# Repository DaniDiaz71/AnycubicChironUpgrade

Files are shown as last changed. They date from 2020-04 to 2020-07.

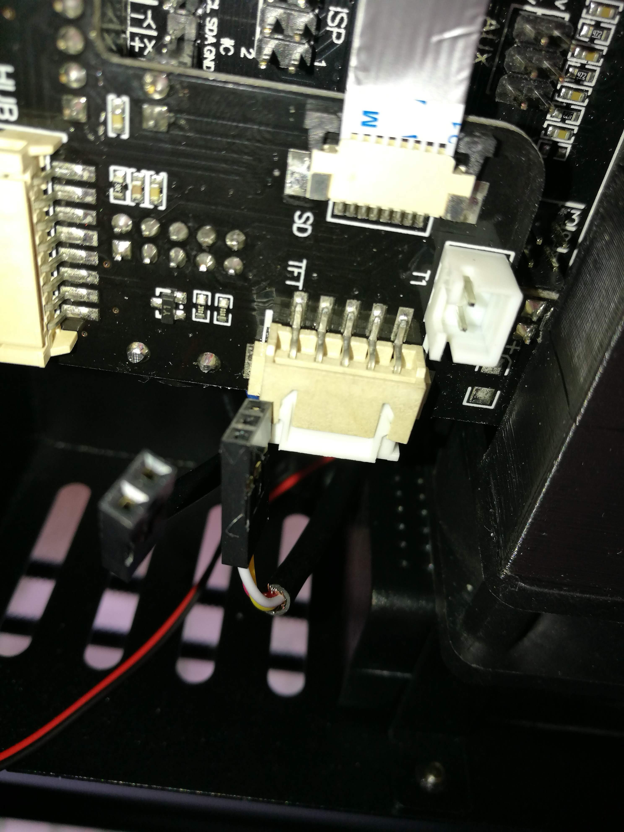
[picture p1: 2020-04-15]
Step 01 - Electronics disassemble/IMG_20200413_175611.jpg

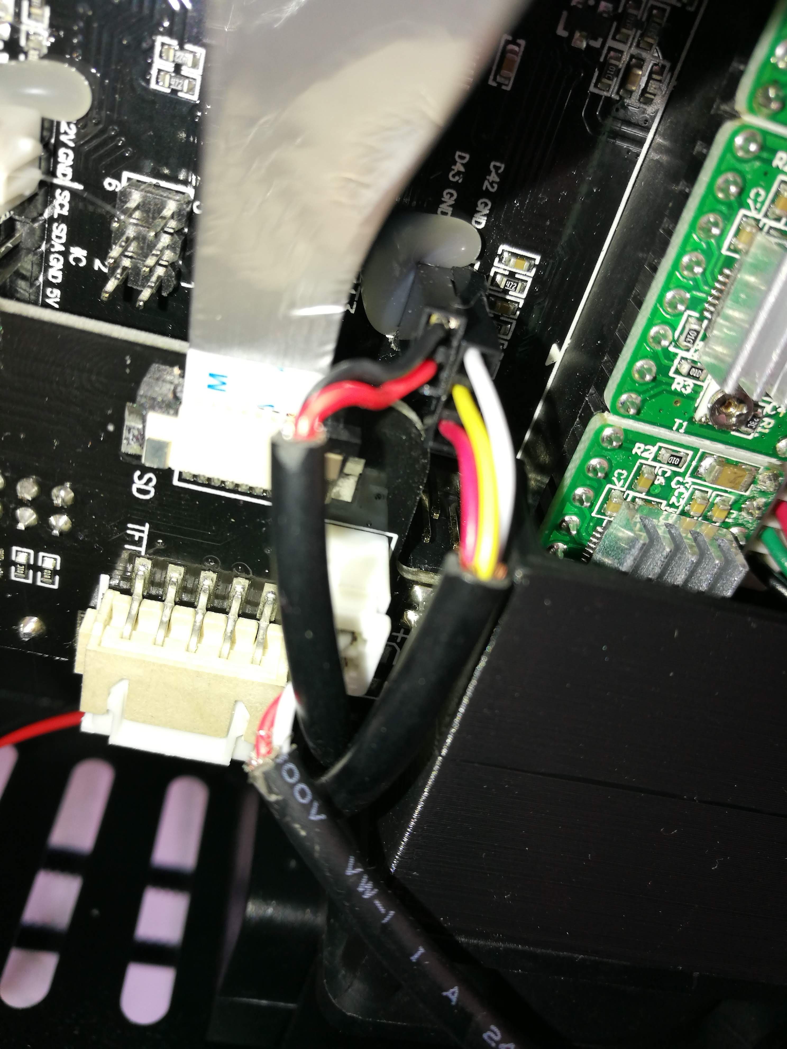
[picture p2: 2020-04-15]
Step 01 - Electronics disassemble/IMG_20200413_175152.jpg

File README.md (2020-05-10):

# AnycubicChironUpgrade

Documentation and other stuff about how upgrade Anycubic Chiron 3D printer from 8 bits to 32 bits electronics, including upgrade stepper drivers to TMC2208. Then i'll configure Marlin.

Work still in progress...

Step 01 - Done!

Step 02 - Done!

Step 03 - Done! 

Step 04 - Done! 

Step in progress - Adding stock display functions to Marlin 2.0.x, there are a lot of work done by dkoch83 at https://github.com/dkoch83/Marlin-1.1.9_Anycubic_Chiron.

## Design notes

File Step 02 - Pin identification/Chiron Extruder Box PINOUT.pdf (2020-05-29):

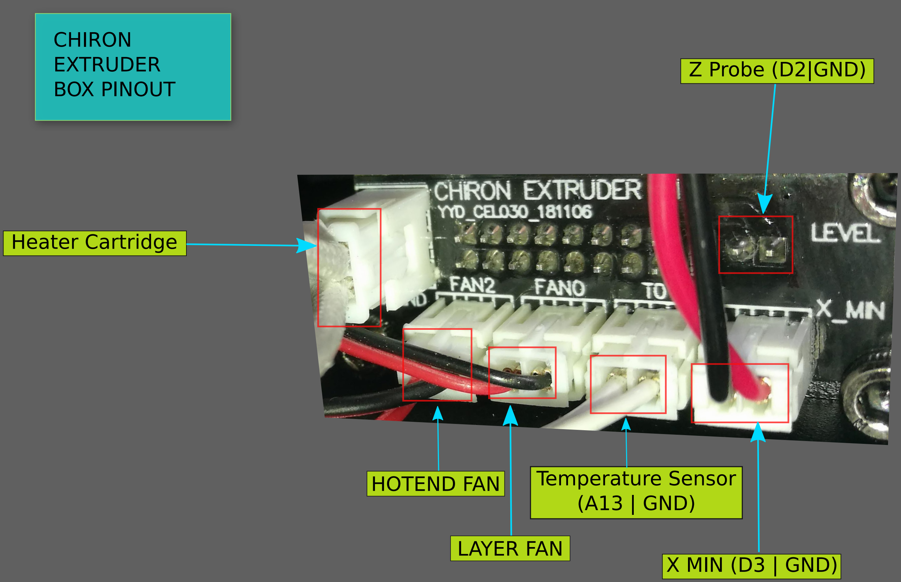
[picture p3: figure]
Heater Cartridge; Z Probe (D2|GND); X MIN (D3 | GND); Temperature Sensor (A13 | GND); LAYER FAN; HOTEND FAN; CHIRON EXTRUDER BOX PINOUT

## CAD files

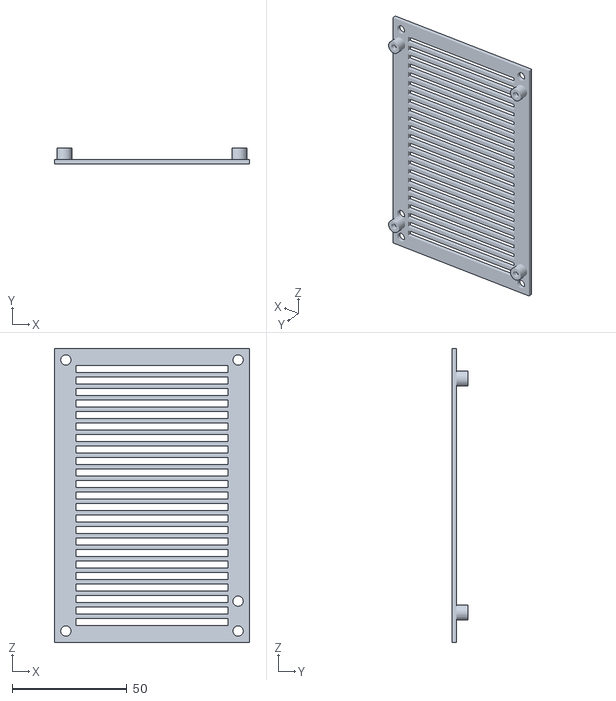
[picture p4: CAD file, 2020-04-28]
Step 03 - Motherboard mount adapter/Chiron Adaptation Mount SKR 1.3 v4.stl
85.0 x 7.00 x 128.0

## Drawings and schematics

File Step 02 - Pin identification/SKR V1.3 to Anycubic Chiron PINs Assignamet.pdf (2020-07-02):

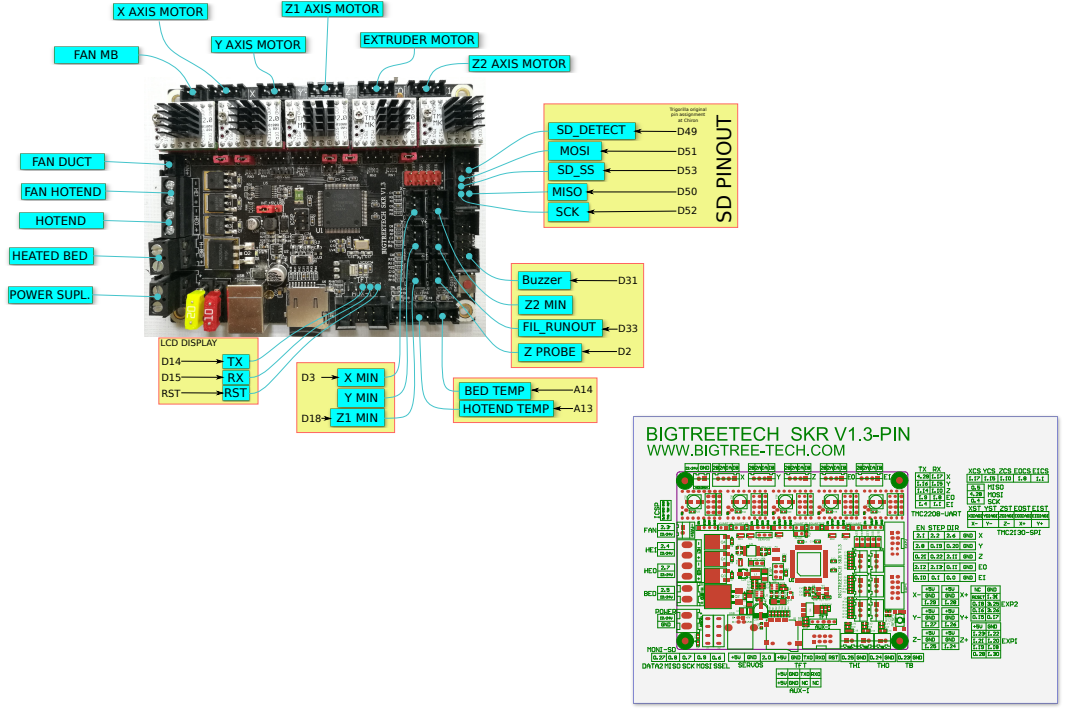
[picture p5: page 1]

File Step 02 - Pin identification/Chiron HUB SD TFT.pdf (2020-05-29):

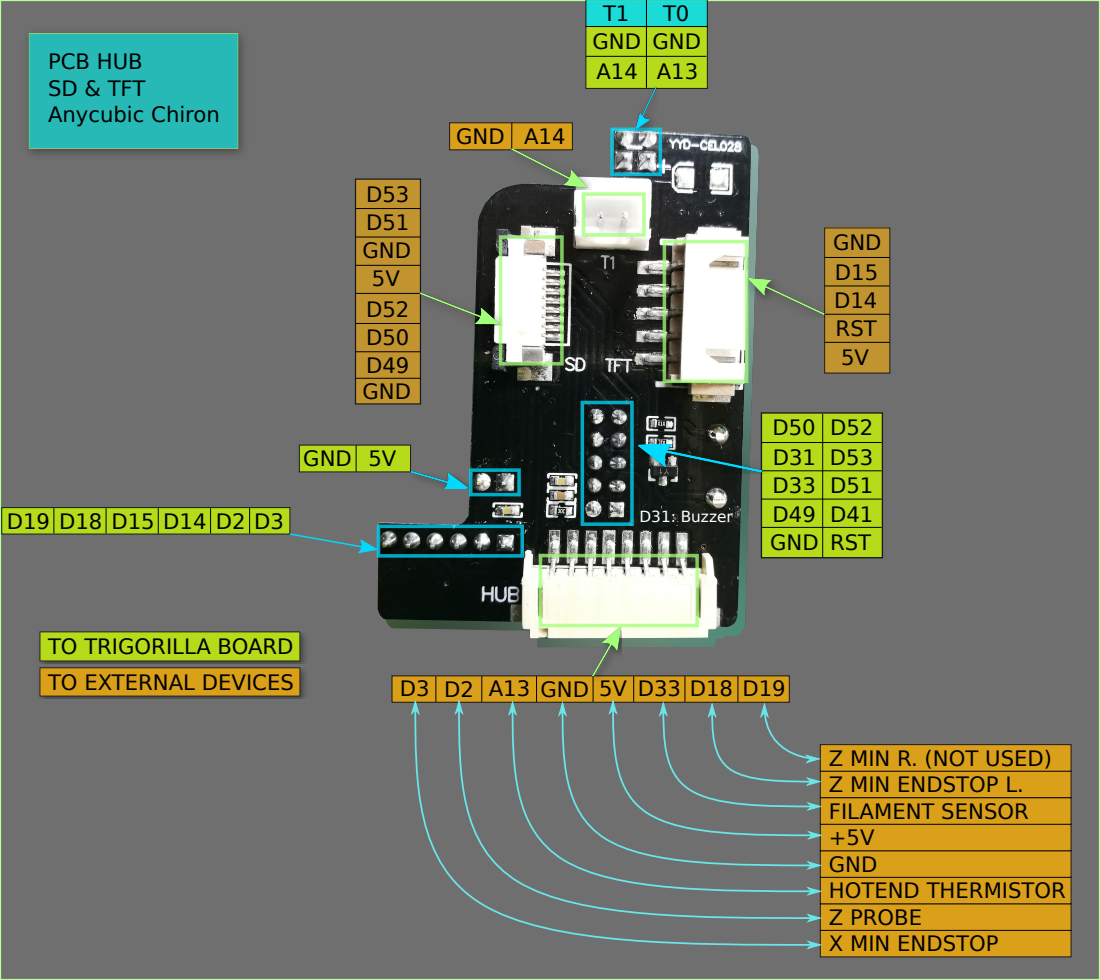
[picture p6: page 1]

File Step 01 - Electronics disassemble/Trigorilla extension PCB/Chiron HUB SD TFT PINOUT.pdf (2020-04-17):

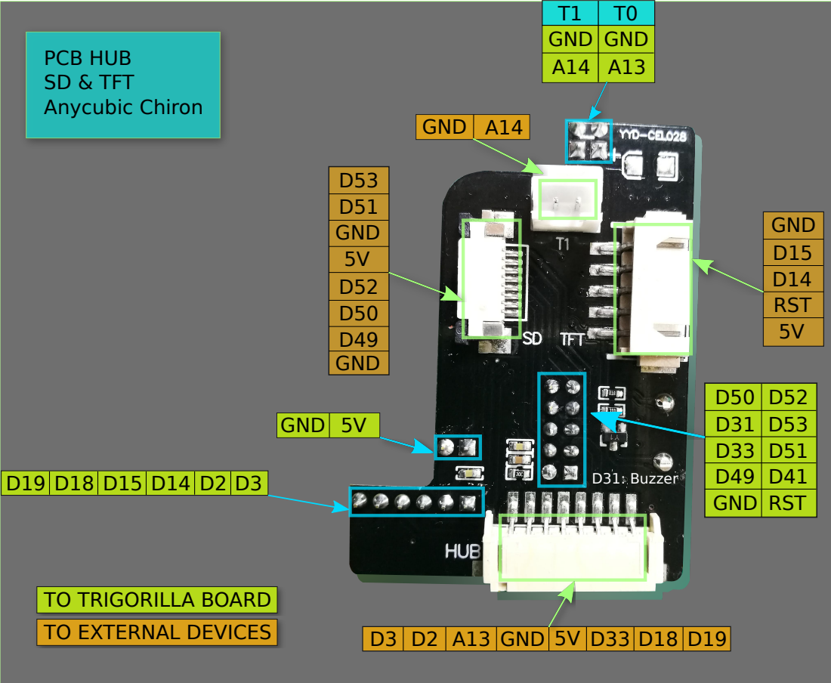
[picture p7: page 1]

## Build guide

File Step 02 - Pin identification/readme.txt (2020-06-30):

Step 02 - Pin identification

In this files are information about non standar pins (TFT, SD, HUB), in particular HUB pin identification.

Chiron HUB SD TFT.svg - Inkscape file with pins from and to Trigorilla board at HUB PCB.
Chiron Extruder Box PINOUT.svg - Inkscape file with pins at hotend box.
New HUB SD TFT PCB to SKR v1.3.fzz - Fritzing file with an small PCB to adapt HUB PCB to SKR v1.3. It's a simple way extract signals.
SKR V1.3 to Anycubic Chiron PINs Assignamet.svg - Inkscape file, pin assingment at SKR v1.3.

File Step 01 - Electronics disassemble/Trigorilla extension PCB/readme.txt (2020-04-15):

This PCB (ref. YYD-CEL028) is over mainboard connecting some pins to SD card reader, heated bed (T1), TFT and other stuff.

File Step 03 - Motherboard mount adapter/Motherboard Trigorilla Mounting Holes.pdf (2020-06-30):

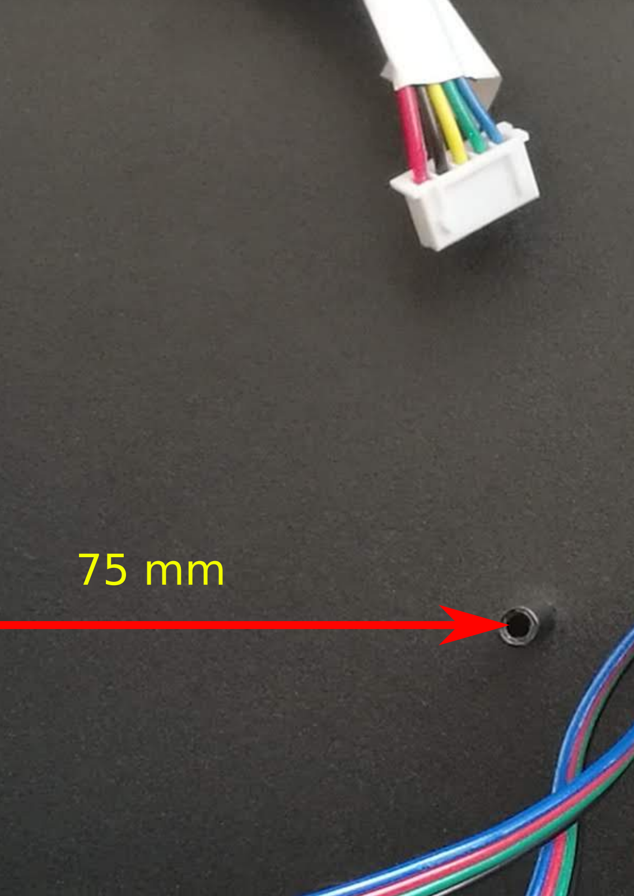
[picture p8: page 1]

75 mm

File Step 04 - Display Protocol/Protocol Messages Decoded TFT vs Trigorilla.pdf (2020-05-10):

### Trigorilla messages after reset

TFT Responds | Trigorilla Sends | Meaning
| | Main board reset
| J12\r\n | Ready

### Periodic update (1.1s) from display to Trigorilla

TFT Request | Trigorilla Response | Meaning
| | A1 → Seted hotend temp (e.g. 200ºC). A2 → Current bed temp (e.g. 50ºC). A3 → Seted bed temp (e.g. 100ºC). A4 → Fan speed (e.g. 1%).

### Query for SD files (Print option)

TFT Request | Trigorilla Response | Meaning
A8' 'S0' '\r\n | J02\r\n | Query [A8] for SD [S0] files but no SD [J02].
| J00\r\n | SD inserted notify [J00]
| J01\r\n | SD extracted notify [J01]
A8' 'S0' '\r\n | | Query for SD files, 3 files in SD.

### Access to Temperature option (Menu>Setup>Temp)

TFT Request | Trigorilla Response | Meaning
A0\r\nA2\r\n

### Access to Motor off option (Menu>Setup>Motor)

TFT Request | Trigorilla Response | Meaning
A19\r\n | \r\n | Turn off motors

### Access to Speed option (Menu>Setup>Speed)

TFT Request | Trigorilla Response | Meaning
| | Query colling fan speed [A4] Query printing rate [A20]
A18' 'S50\r\n | \r\n
A20' 'S120\r\n | \r\n

### Access to Home (Menu>Tools>Auto Home)

TFT Request | Trigorilla Response | Meaning
A21' 'C\r\n | | Home all axis
A21' 'X\r\n | | Home X axis
A21' 'Y\r\n | | Home Y axis
A21' 'Z\r\n | | Home Z axis

### Access to Home (Menu>Tools>Cooling)

TFT Request | Trigorilla Response | Meaning
A25\r\n | J12\r\n | Set hotend cooling

### Access to Home (Menu>Tools>Move Axis)

TFT Request | Trigorilla Response | Meaning
A21' 'C\r\n | | Home all axis
| \r\n | Move X axis 10mm; Speed L
| \r\n | Move X axis -10mm; Speed L
| \r\n | Move X axis 10mm; Speed M
| \r\n | Move X axis -10mm; Speed M
| \r\n | Move X axis 10mm; Speed H
| \r\n | Move X axis -10mm; Speed H
| \r\n | Move Y axis 10mm; Speed L
| \r\n | Move Y axis -10mm; Speed L
| \r\n | Move Y axis 10mm; Speed M
| \r\n | Move Y axis -10mm; Speed M
| \r\n | Move Y axis 10mm; Speed H
| \r\n | Move Y axis -10mm; Speed H
| \r\n | Move Z axis 10mm; Speed L
| \r\n | Move Z axis -10mm; Speed L
| \r\n | Move Z axis 10mm; Speed M
| \r\n | Move Z axis -10mm; Speed M
| \r\n | Move Z axis 10mm; Speed H
| \r\n | Move Z axis -10mm; Speed H
A22' 'X' '+1F1000\r\n | \r\n | Move X axis 1mm; Speed L
A22' 'X' '-1F1000\r\n | \r\n | Move X axis -1mm; Speed L
A22' 'X' '+1F3000\r\n | \r\n | Move X axis 1mm; Speed M
A22' 'X' '-1F3000\r\n | \r\n | Move X axis -1mm; Speed M
A22' 'X' '+1F5000\r\n | \r\n | Move X axis 1mm; Speed H
A22' 'X' '-1F5000\r\n | \r\n | Move X axis -1mm; Speed H
A22' 'Y' '+1F1000\r\n | \r\n | Move Y axis 1mm; Speed L
A22' 'Y' '-1F1000\r\n | \r\n | Move Y axis -1mm; Speed L
A22' 'Y' '+1F3000\r\n | \r\n | Move Y axis 1mm; Speed M
A22' 'Y' '-1F3000\r\n | \r\n | Move Y axis -1mm; Speed M
A22' 'Y' '+1F5000\r\n | \r\n | Move Y axis 1mm; Speed H
A22' 'Y' '-1F5000\r\n | \r\n | Move Y axis -1mm; Speed H
A22' 'Z' '+1F1000\r\n | \r\n | Move Z axis 1mm; Speed L
A22' 'Z' '-1F1000\r\n | \r\n | Move Z axis -1mm; Speed L
A22' 'Z' '+1F3000\r\n | \r\n | Move Z axis 1mm; Speed M
A22' 'Z' '-1F3000\r\n | \r\n | Move Z axis -1mm; Speed M
A22' 'Z' '+1F5000\r\n | \r\n | Move Z axis 1mm; Speed H
A22' 'Z' '-1F5000\r\n | \r\n | Move Z axis -1mm; Speed H
A22' 'X' '+0.1F1000\r\n | \r\n | Move X axis 0.1mm; Speed L
A22' 'X' '-0.1F1000\r\n | \r\n | Move X axis -0.1mm; Speed L
A22' 'X' '+0.1F3000\r\n | \r\n | Move X axis 0.1mm; Speed M
A22' 'X' '-0.1F3000\r\n | \r\n | Move X axis -0.1mm; Speed M
A22' 'X' '+0.1F5000\r\n | \r\n | Move X axis 0.1mm; Speed H
A22' 'X' '-0.1F5000\r\n | \r\n | Move X axis -0.1mm; Speed H
A22' 'Y' '+0.1F1000\r\n | \r\n | Move Y axis 0.1mm; Speed L
A22' 'Y' '-0.1F1000\r\n | \r\n | Move Y axis -0.1mm; Speed L
A22' 'Y' '+0.1F3000\r\n | \r\n | Move Y axis 0.1mm; Speed M
A22' 'Y' '-0.1F3000\r\n | \r\n | Move Y axis -0.1mm; Speed M
A22' 'Y' '+0.1F5000\r\n | \r\n | Move Y axis 0.1mm; Speed H
A22' 'Y' '-0.1F5000\r\n | \r\n | Move Y axis -0.1mm; Speed H
A22' 'Z' '+0.1F1000\r\n | \r\n | Move Z axis 0.1mm; Speed L
A22' 'Z' '-0.1F1000\r\n | \r\n | Move Z axis -0.1mm; Speed L
A22' 'Z' '+0.1F3000\r\n | \r\n | Move Z axis 0.1mm; Speed M
A22' 'Z' '-0.1F3000\r\n | \r\n | Move Z axis -0.1mm; Speed M
A22' 'Z' '+0.1F5000\r\n | \r\n | Move Z axis 0.1mm; Speed H
A22' 'Z' '-0.1F5000\r\n | \r\n | Move Z axis -0.1mm; Speed H

### Access to Home (Menu>Tools>Preheat)

TFT Request | Trigorilla Response | Meaning
A23\r\n | OK\r\n | Preheat PLA
A24\r\n | OK\r\n | Preheat ABS

### Access to Home (Menu>Tools>Filament)

TFT Request | Trigorilla Response | Meaning
| | Filament In/Out; If temp. hotend<230ºC
A22' 'E' '+50F700\r\n | \r\n | Filament In; If temp. hotend>230ºC. Every 1,1s
A22' 'E' '-50F700\r\n | \r\n | Filament Out; If temp. hotend>230ºC. Every 1,1s
A19\r\n | \r\n | Stop
A0\r\nA1\r\n | | Periodic hotend temp. update, every 1,1s

### Access to Home (Menu>Tools>Info)

TFT Request | Trigorilla Response | Meaning
A33\r\n | J33' 'V1.3.0\r\n | Ask for firmware version. Only updates version in display, remaning data is hardcoded.

### Access to Home (Menu>Tools>Level>Probing)

TFT Request | Trigorilla Response | Meaning
A30S\r\n | | Start probing process. First Trigorilla sends J26 and J25 85 secods after.

### Access to Home (Menu>Tools>Level>Advanced setting)

TFT Request | Trigorilla Response | Meaning
A31G\r\n | | Access to ‘Advanced setting’ option. Trigorilla sends Z offset (e.g. -17.65mm)
A29' 'X0' 'Y0\r\n
A29' 'X4' 'Y4\r\n
| | Set offset point 25 (X4, Y4), TFT displays 220.12
A31S0.05\r\n | A31V' '-17.60\r\n\r\n | Set offset (e.g. +0.05) to ALL points. TFT displays offset (-17.60).
A31S-0.05\r\n | A31V' '-17.65\r\n\r\n | Set offset (e.g. -0.05) to ALL points. TFT displays offset (-17.65).
A31D\r\n | \r\n | Push OK to confirm changes.

All these messages were captured using a digital analyzer (115200 bitrate), so it’s real information between Anycubic TFT display and

Trigorilla board. You can contrast it with Anycubic firmware 1.3.0 at Github https://github.com/ANYCUBIC-3D/ANYCUBIC_CHIRON

J17\r\n

A0\r\n
A1\r\n
A2\r\n
A3\r\n
A4\r\n

A0V' '' '31\r\n
A1V' '200\r\n
A2V' '' '50\r\n
A3V' '100\r\n
A4V' '1\r\n

A0 → Current hotend temp (e.g. 31ºC).

FN' '\r\n
STRING~1.GCO\r\n
String' 'Test' '4.gcode\r\n ARTICU~1.GCO\r\n
Articulated_Butterfly.gcod\r\n 3DBENC~1.GCO\r\n
3DBenchy.gcode\r\n
END\r\n
A0V' '' '31\r\nA2V' '' '50\r\n | Current hotend and bed temp (e.g. 31ºC/50ºC).. This info it’s periodic (1.1s)
A16' 'S200\r\n
A17' 'S50\r\n
| Set hotend temp (e.g. 200ºC) [A16]. Set bed temp (e.g. 50ºC) [A17].

A4\r\n
A20\r\n

A4V' '1\r\n
A20V' '100\r\n
Set fan speed (e.g. 50%) [A18]
Set printing rate speed (e.g. 120%) [A20]

A22' 'X' '+10F1000\r\n
A22' 'X' '-10F1000\r\n
A22' 'X' '+10F3000\r\n
A22' 'X' '-10F3000\r\n
A22' 'X' '+10F5000\r\n
A22' 'X' '-10F5000\r\n
A22' 'Y' '+10F1000\r\n
A22' 'Y' '-10F1000\r\n
A22' 'Y' '+10F3000\r\n
A22' 'Y' '-10F3000\r\n
A22' 'Y' '+10F5000\r\n
A22' 'Y' '-10F5000\r\n
A22' 'Z' '+10F1000\r\n
A22' 'Z' '-10F1000\r\n
A22' 'Z' '+10F3000\r\n
A22' 'Z' '-10F3000\r\n
A22' 'Z' '+10F5000\r\n
A22' 'Z' '-10F5000\r\n

A16' 'C230\r\n

A0V' '230\r\nA1V' '' '' '0\r\n

J26\r\n
J25\r\n

A31V' '-17.65\r\n\r\n
A29V' '2799.50\r\n | Get info point 1 (X0,Y0), Trigorilla sends offset (displays 27.99)
A29V' '21987.50\r\n | Get info point 25 (X4,Y4), Trigorilla sends offset (displays 219.87)
A34' 'X4' 'Y4' 'V22012\r\n

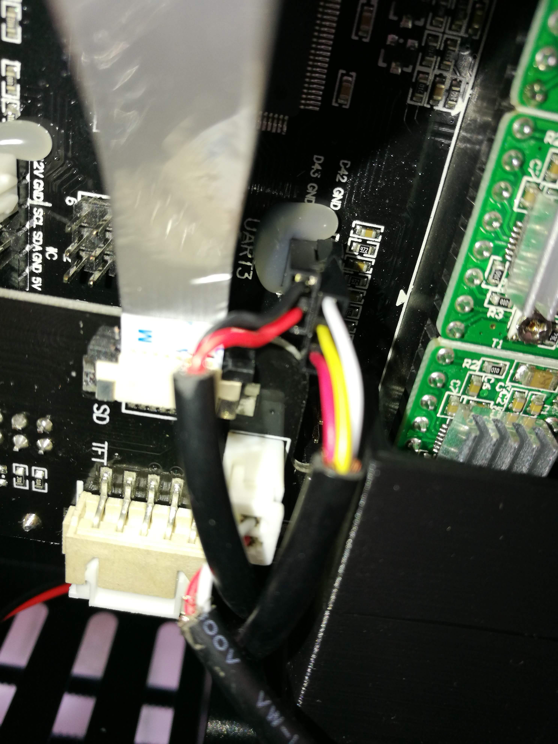
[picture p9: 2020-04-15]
Step 01 - Electronics disassemble/IMG_20200413_175147.jpg

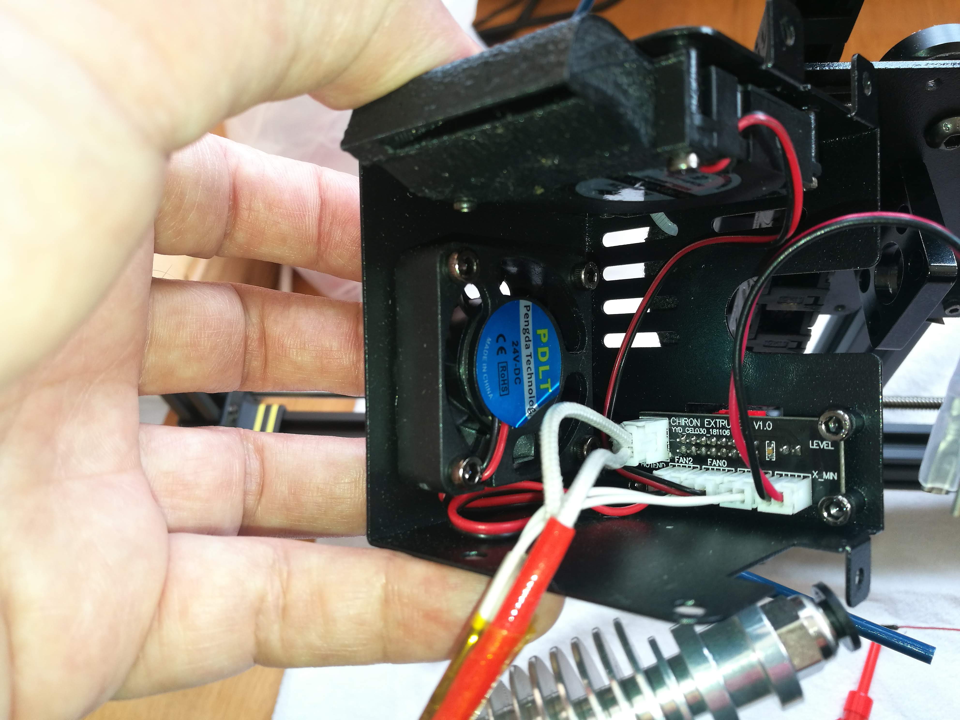
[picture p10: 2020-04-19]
Step 01 - Electronics disassemble/IMG_20200418_135820.jpg

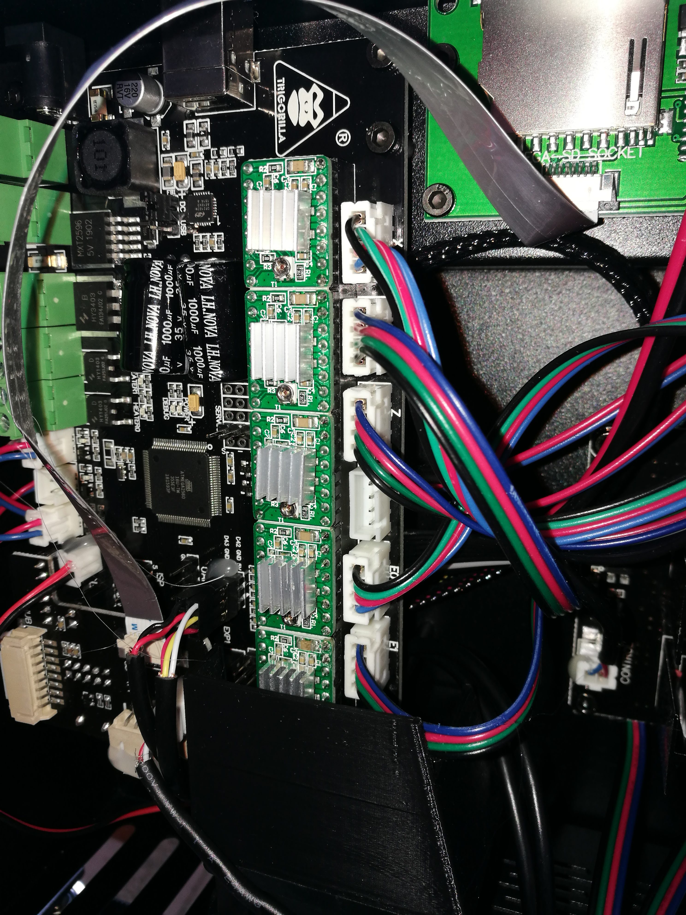
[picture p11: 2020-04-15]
Step 01 - Electronics disassemble/IMG_20200413_174305.jpg

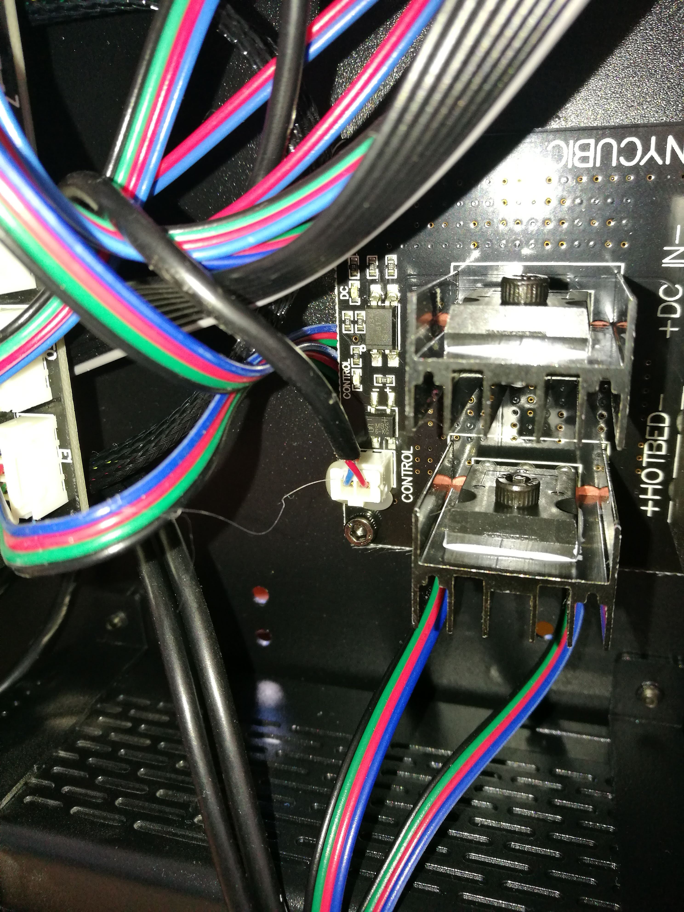
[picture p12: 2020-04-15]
Step 01 - Electronics disassemble/IMG_20200413_182542.jpg

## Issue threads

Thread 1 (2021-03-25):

Hi, DaniDiaz.

samuf92, 2021-03-25:
I really interested to get this change on my Chiron too, actually i use Coolio Marlin 2.0 version for Chiron
https://github.com/coolio986/Marlin_2.0.x_Anycubic_Chiron

Have you found a way tu use the default chiron display with SKR board??

DaniDiaz71, 2021-03-25:
Hi! I was able to do it and now it's working but unfortunately before upload source code to Github my hard disk died :( So the only thing i have it's the compiled hex file. I can share it but I'm not sure if this will work on any other printer because i have rewired some stuff.
Anyway check Marlin last version because I think some developers include Chiron stock display to Configuration.h. Last version has this line: //#define ANYCUBIC_LCD_CHIRON so I guess there should be stock display support but I didn't try it. Drop me a line if you test it :)
Best regards!

Closed 2023-02-21.

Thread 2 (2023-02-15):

Hey! Quick question about how you have your hotbed wired.

xontinuity, 2023-02-15:
So I'm going to be doing this conversion for my Chiron but to an SKR v1.4.

Basically, my Chiron has a MOSFET separate from the OG TriGorilla with a control wire to turn it on and off (this is for the hotbed).

Does your Chiron have this, and is the output from the hotbed terminal on the SKR you have pictured run to that control input?

Thanks!

PS: If you had stated this somewhere in the repository I missed it. If you did then sorry in advance for this redundant question... I just want to be certain I get everything set up properly!

DaniDiaz71, 2023-02-21:
Hi,

Did you check all my pictures? I think there's a photo where you can see both mostef.

BR.

Closed 2023-02-21.

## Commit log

2020-04-17 HUB PCB PINOUT
2020-04-19 Images update
    [New HUB SD TFT PCB to SKR v1.3.fzz]
2020-04-21 Add files via upload
    Minor update
    [New HUB SD TFT PCB to SKR v1.3.fzz]
2020-04-28 Add files via upload
    Motherboard adaptation mount
    [Chiron Adaptation Mount SKR 1.3 v4.stl]
2020-05-10 Step 04
    [Protocol Messages Decoded TFT vs Trigorilla.ods]
2020-05-22 Adding new PCB HUB Extension
    [New HUB SD TFT PCB to SKR v1.3.fzz]
2020-06-01 New pin assigment at SKR v1.3
